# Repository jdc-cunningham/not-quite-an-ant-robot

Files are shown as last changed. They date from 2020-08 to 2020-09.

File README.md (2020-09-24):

# About
My first legged robot. This was not really designed in terms of using math with regard to torque on servos/current draw/etc... as a result it works best on flat surfaces. The motion of the body is also not great since it can't really lift the legs straight up, rather just swing them out then in an arc to move. At this time I'm still working on the control system by phone, I have an ESP8266-01 and it has a websocket server that my phone connects to, then by serial between the ESP and Arduino I can send commands to run specific gaits to move the robot. At the moment I only have some forward gaits, I am still working on improving/writing better "abstractions" for the code eg. passing in an array of servos/ranges into a function to move the servos at the same time. Right now I just have a bunch of loops as a proof of concept.

This is not intended to be replicated, I mean all the parts are here and I'll provide estimates on print but it's not a good design.

This project has been in progress for at least a week, I don't have a repo history because I published my WiFi SSD credentials in the original private repo.

# Status
Pretty much done/abandoned since the body is too weak and dumb to do anything more. It has a run time I could venture to say up to 2.5 hrs on the specified specs but that's absolutely dry. I did a 30 minute non-stop run and it pulled about 500mAh from the battery. This is at 5.5V at the step down buck converter as I was trying to have the servos use around 4.8V. It seems to perform better here than 6V as it was initially. The next project I'm working on the hybrid sensor pack will weigh at least 6oz and I put an 8oz weight on top of the robot and it could not carry it... so that's why I'm kind of going to abandon this robot as is since it's a disappointment in terms of the build/no brain.

# The vision/concept

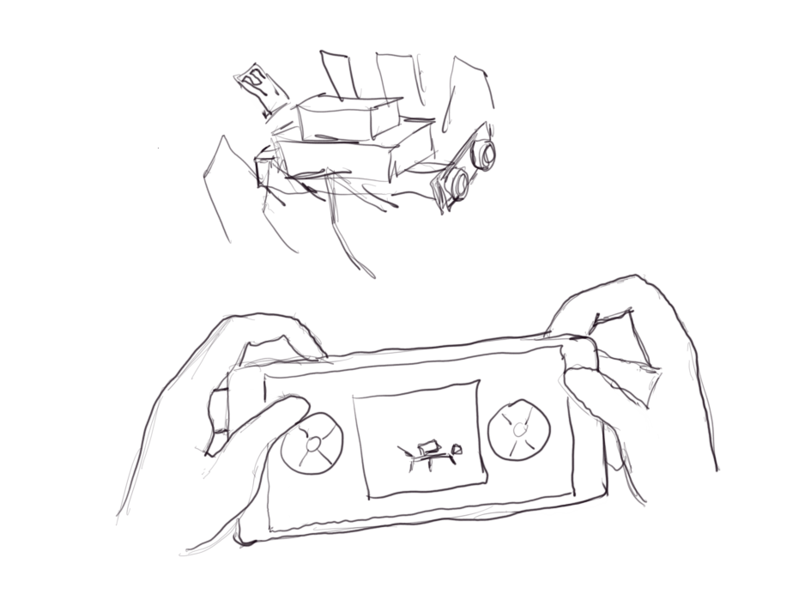
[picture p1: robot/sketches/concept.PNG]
drawing of concept


# Actual - not quite as I foresaw
### Reasons being:
- too slow to control manually, does not have 4 axis of motion only 2(forward/back, left/right)
- telemetry would have been easy with what I'm doing and the embedded `WebGL` aspect would have been overkill as well as a little animation for the controller. Mostly though changing directions, this robot is too weak/stupid to be useful, I can't leave it alone to map a room without thinking it'll get stuck and burn a servo out.

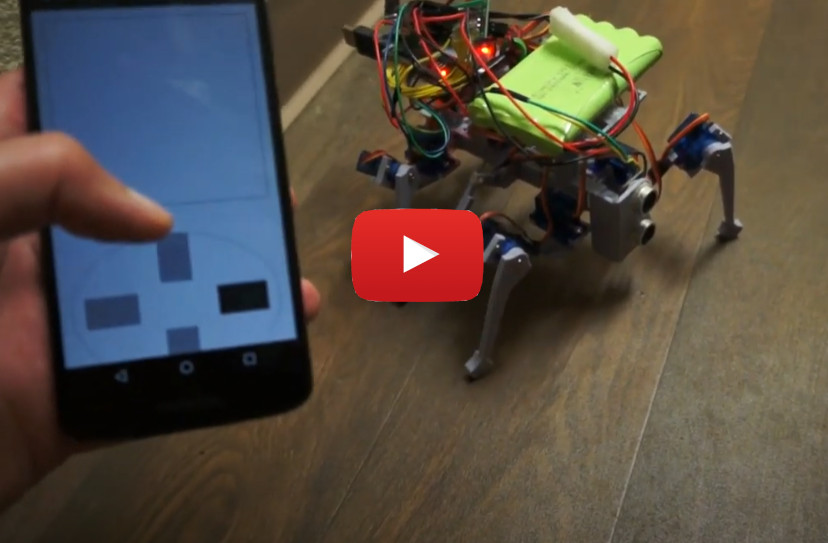
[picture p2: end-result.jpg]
end result (https://youtu.be/18nqn2tWNEw?t=28)


Later on it turns out that having a controller like this while cool is also not practical as the robot is so slow, I'll still build it but it'll be like a "heading hold" type of control.

current build

I did just throw a thing on top to hold the electronics, ideally the CG would be lower, there is clearance below the body, especially since now it's not intended to work on carpet which mine is a little deep eg. `1/2 in` long threads.

While I did design the legs like this(back set not mirrored), they are actually technically "backwards"/not symmetrical... so it has a forward-cg to compensate.

current build side

It has a middle servo pretty much for balance, when it moves forward the middle servo lifts up the middle legs. Anyway with this design as a result I can't do the full tripod-gait, I have some type of modified trypod gait going on. Initially I had a wave-type gait going, where one leg moved at a time but I think that's too slow. It is nuts how much current all the servos pull. I had to use a 2A wall power supply and hardly any of my batteries would work(too heavy/not enough current).

current build back view

Here the servos are not moving very fast(`10ms delay`) and a 2 second overally delay between the forward motion gait see [here](./robot/code/test/all_servos/all_servos.ino).

## Note: it's not as slow as you see above

The servo speed is just set slow there, [here it is near full speed](https://www.youtube.com/watch?v=y_KfgiUq9XE)

# Parts list

- ($18.69 for 10) 9g servo (x9)
- ($15.98 for 3) Arduino Nano
- ($12.98 for 4) ESP8266-01
- ($9.59 for 5) HC-SR04 ultrasonic sensor
- ($12.99 for 5) 5V buck converter for battery (can use UBEC maybe linear regulator as well)
- ($7.85 for 12) 3.3V linear regulator (x2)
- 10K resitor
- ($17.99) 9.6v 8cell 2400mAh NiMh battery pack
- solderable breadboards
- breadboards
- breadboard wires
- 3D printer/filament
- hot/super glue

## Total Unit cost estimate: $50.00
(not including tools eg. 3D printer($200))

### Note: can also use a 7.2v 2 cell battery
After lowering the voltage the servos operated at, it can run on a 2 cell li-ion, I'm using a 2 cell 2600mAh now. It's much lighter(<3oz vs. 6oz)
That gives some extra weight that could be carried.

# Schematic

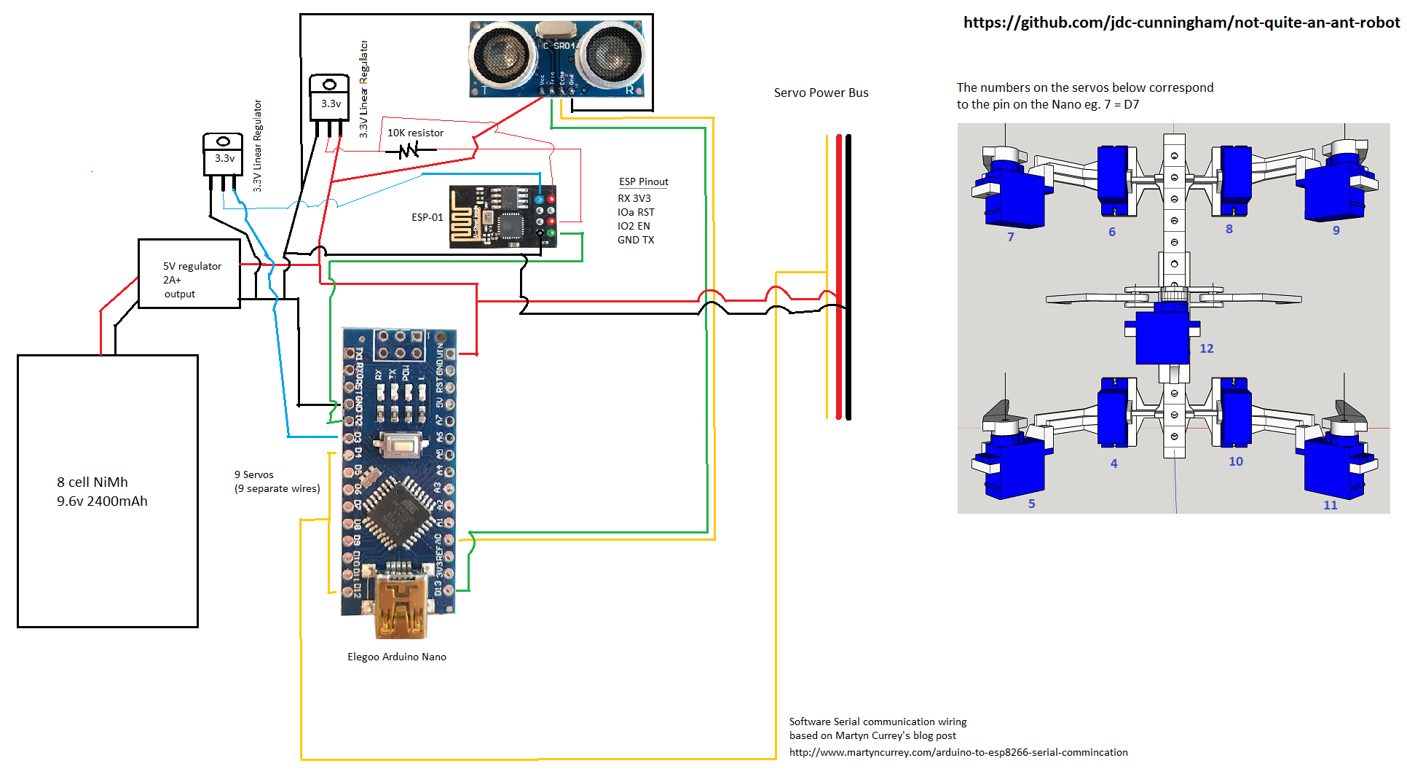
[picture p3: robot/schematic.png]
ms paint wiring diagram


# Feature Completion

- [x] physical body
- [x] basic socket to serial communication
- [ ] rest of the gaits
    - [x] backwards
    - [ ] sideways (crab) - attempt called sway in code
        - doesn't really work(need to be on smooth surface)
    - [x] rotate
    - [ ] roll
        - similar to crab walk, again problem of servos being weak
- [x] mobile controller
    - very basic design, spent like 2 hours
- [ ] add IMU (9-axis)
    - not done on this robot, maybe added later assuming light enough
- [x] add ultrasonic sensor on front
    - current code intercepts commands and makes robot turn left if something is within 7" of front

# Print times (0.2mm quality 20% infill)
- 49 mins main servo mount for swivel arms
- 2 hrs 42 mins middle lift legs
- 4 hrs 20 mins top group
- 3 hrs 14 mins test stand
- 1 hr 29 mins outer pitch legs
- 1 hr 26 mins 1 swivel arm
- 1 hr 34 mins main stick with holes

## Update
I would suggest printing the legs(pitch and swivel) thicker as they experience the most stress. This is only really a problem on carpet. I am printing out these foot cups which may help alleviate the stress on the legs but still it may be a good idea to increase that thickness(will need to reslice).

# Software

The parts were designed with Google SketchUp. I used a plugin to export the STL file(as well as a solid part inspector plugin) then used Cura to slice the parts. Take note of parts that need supports, you have to turn that on in Cura. Parts are printed with a Creality Ender 3 Pro.

# Warning

The servo horn spline I have here is bad, they slip. I traced/made my own from a photo I took. I ended up having to use long screws and super glue to try and make them not slip. Also the design is generally bad where the servos are directly holding the load vs. just transfering motion. And overall the design is bad as I mentioned with how it can move. I think you need more servos but it's nuts thinking each leg would have at least 3 servos and a true hexapod would have 18 servos right there.

# Thoughts

Overall it is a fun project, learned a lot. It has a ways to go code wise and will serve as a platform for other work.

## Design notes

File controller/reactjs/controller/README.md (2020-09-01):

# About the controller
This is a basic controller, I created a different version initially but triangles in html/css are kind of a hack so the last triangle overlaps the rest... problems with clicks. It's not an impossible thing to solve eg. use SVG or background images, etc... but yeah. Also the math since I didn't have something to bind clicks to, this is not just a quadrant it's a diagonal thing going on for the original design below. I ended up just going with a basic `+` style controller. It's also not responsibly styled or anything, I probably spent 2 hrs on this controller so yeah it's trash but it does work. When the robot is turned on __first__ your phone or computer that's looking at the deployed static files of this controller will connect to the robot and steer it. The ultrasonic sensor onboard will interrupt your command and avoid an obstacle if it detects one within 7 inches(roughly half the box the robot takes up/uses to rotate).

Also I have not gotten to the interface/telemetry aspect. It's kind of pointless at this time for this project since I can't leave this project alone(it can get stuck, flip over, etc... strain the servos). For example the center servo got so hot(not sure if it was a dud or not, hasn't happened since) but it got so hot it started to melt the plastic mount(3D printed).

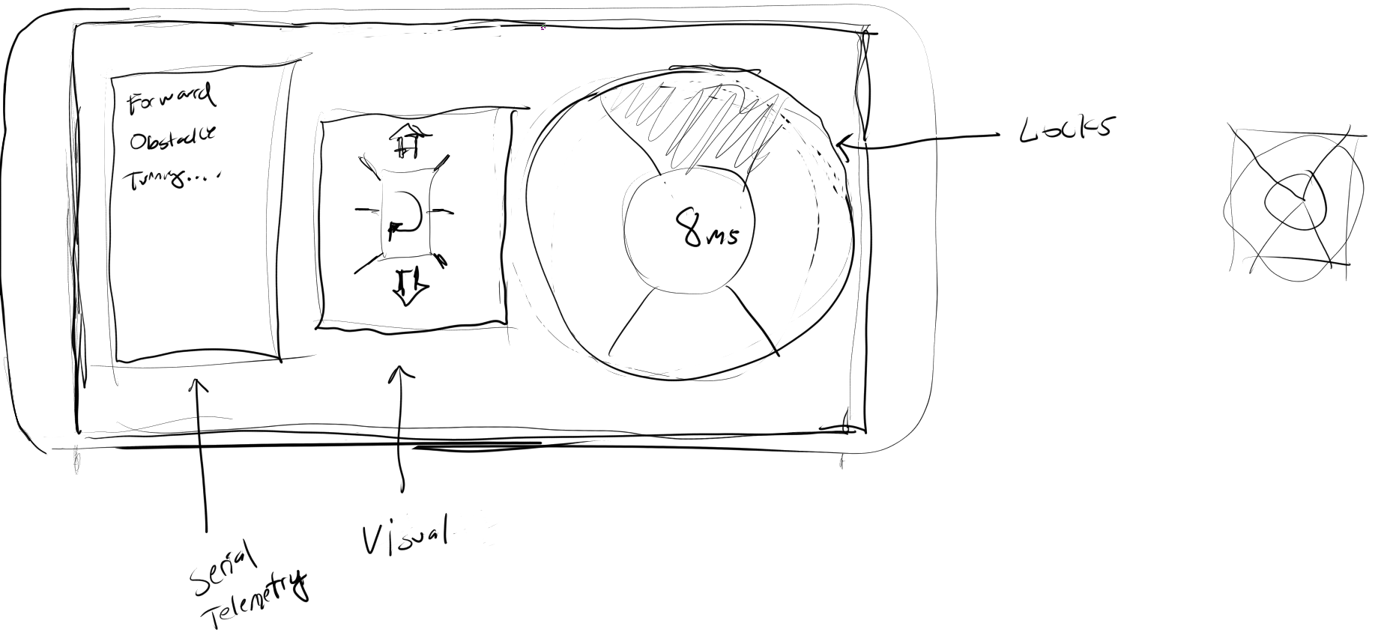
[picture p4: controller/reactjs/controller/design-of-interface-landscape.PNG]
controller thoughts


Anyway instead of the above you just have this lol. But yeah some telemetry would be possible by the serial onboard but since it's software serial at `115200` (trash data) you'd probably have to do some enumeration like I did which I don't know how useful that is.

The other aspect that's missing here is a front-end IP scanner because the IP may change if your router re-assigns the device. So you'd have to manually put in existing/known ip's then the mobile controller would scan the possible open ones and try to connect by socket.

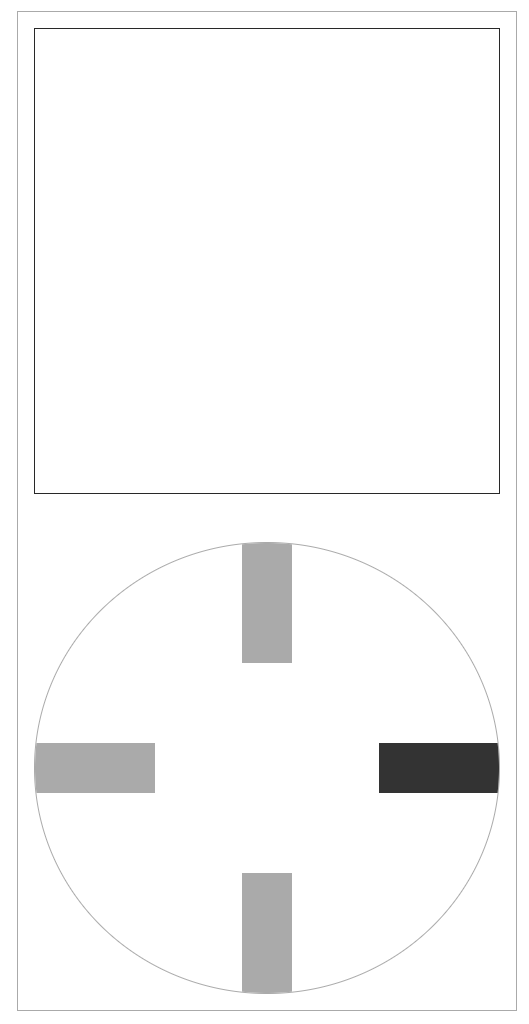
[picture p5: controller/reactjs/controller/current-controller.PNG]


# To use
Anyway if anyone actually tries to use this. You'll have to change the IP in the `App.js` to match your ESP's IP that's hosting the websocket server. Then do `npm run build` that'll generate your static files(assumes you have `node/npm/npx` installed haha). I can see how you make "useable code".

This project was bootstrapped with [Create React App](https://github.com/facebook/create-react-app).

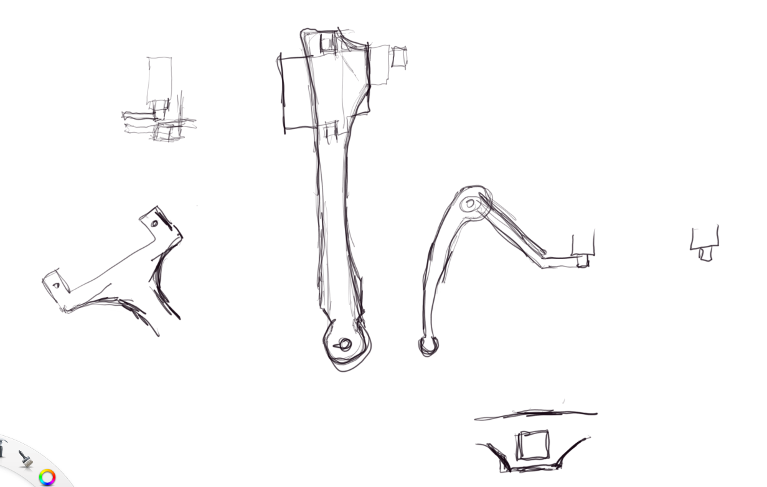
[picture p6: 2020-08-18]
robot/sketches/leg-design.PNG

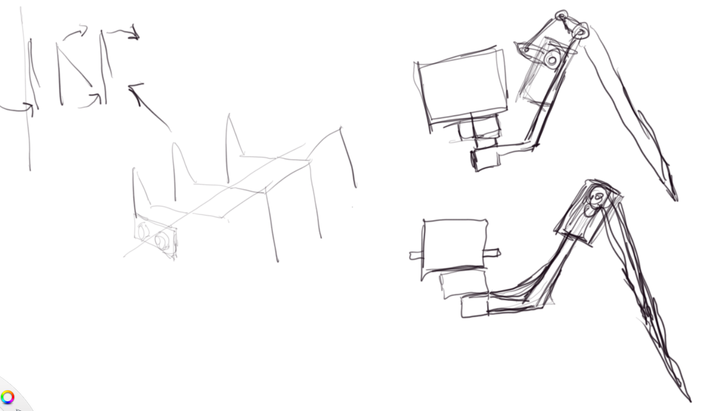
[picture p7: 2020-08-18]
robot/sketches/concept2.PNG

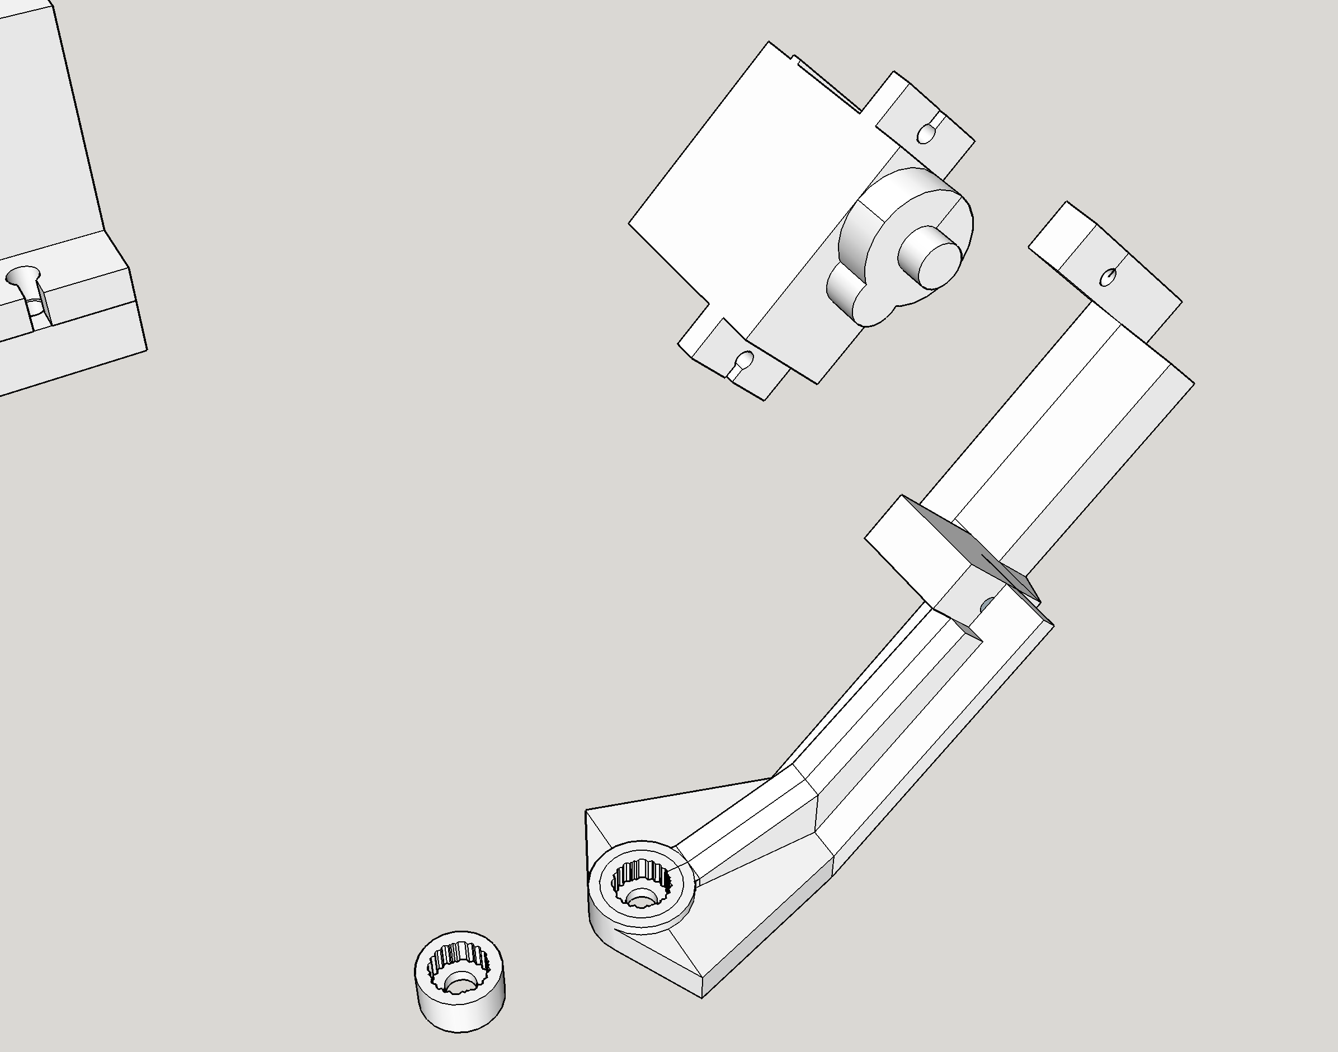
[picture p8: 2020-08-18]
robot/screenshots/no-way.png

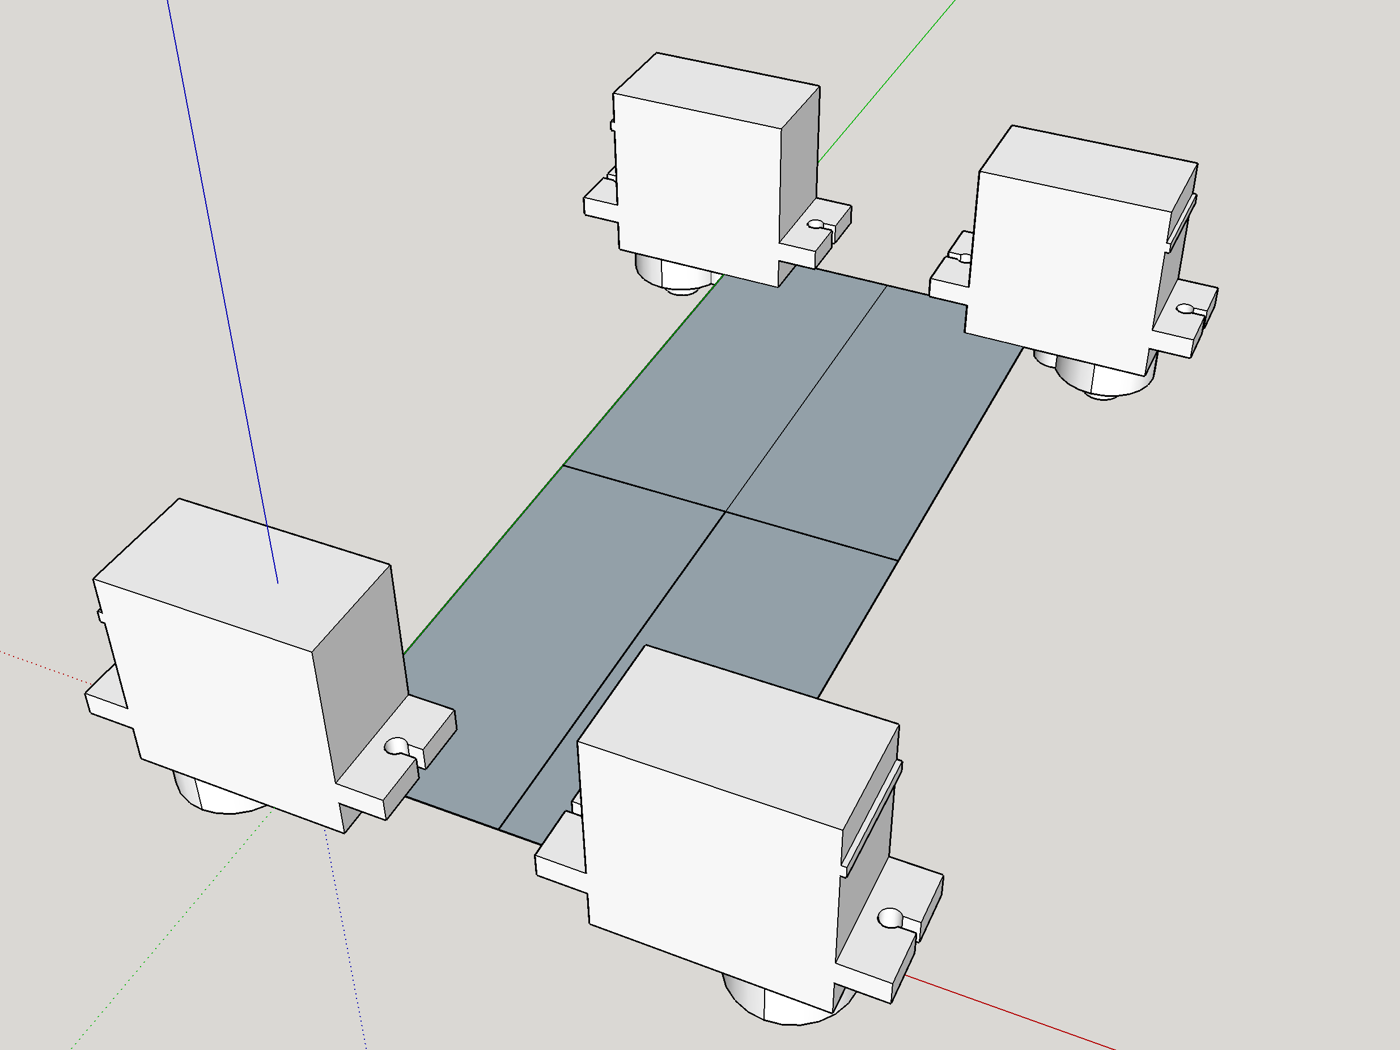
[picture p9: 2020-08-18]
robot/screenshots/chasis-config-1.png

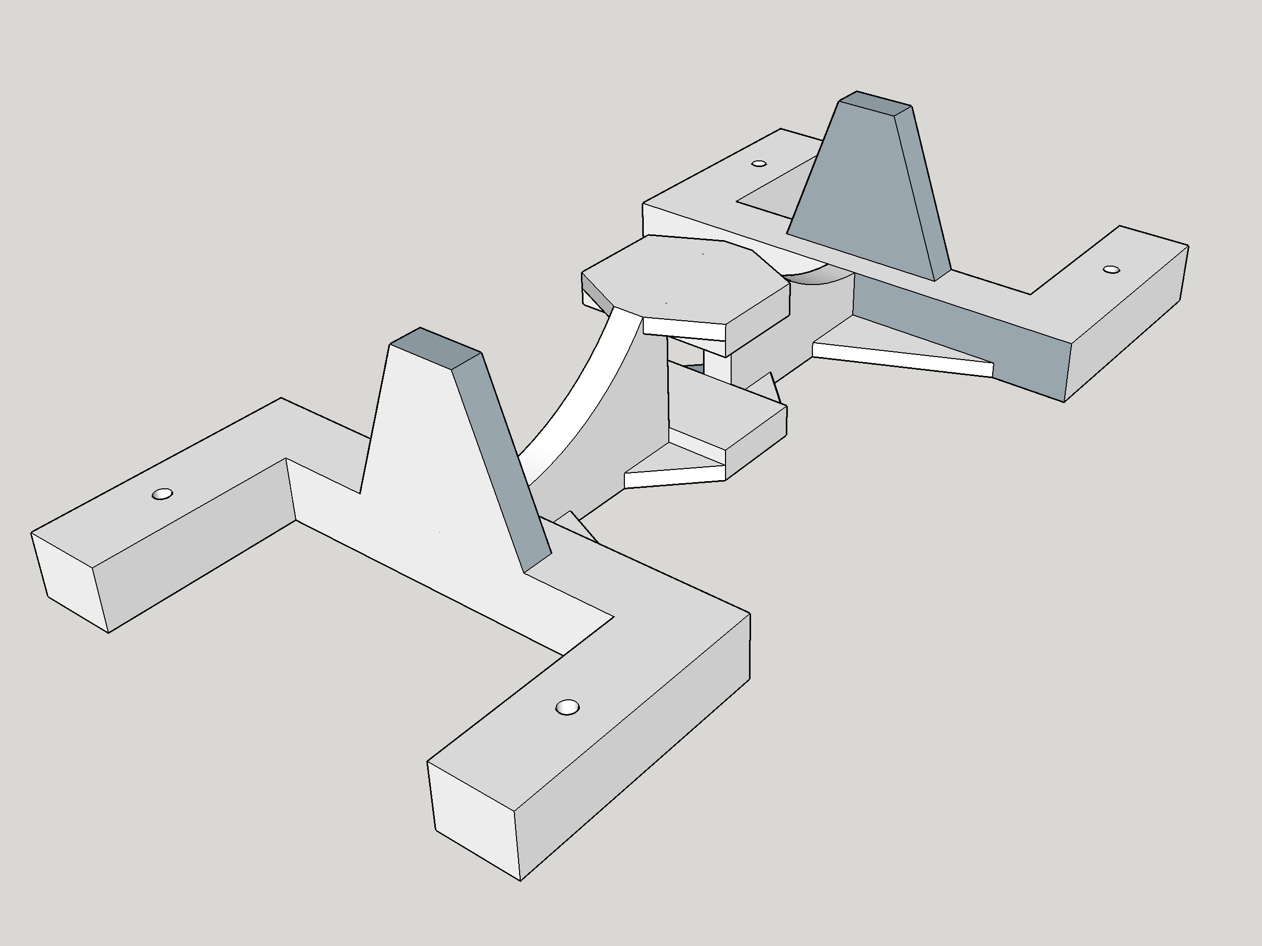
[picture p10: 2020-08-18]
robot/screenshots/horizontal-swivel-servo-mount.png

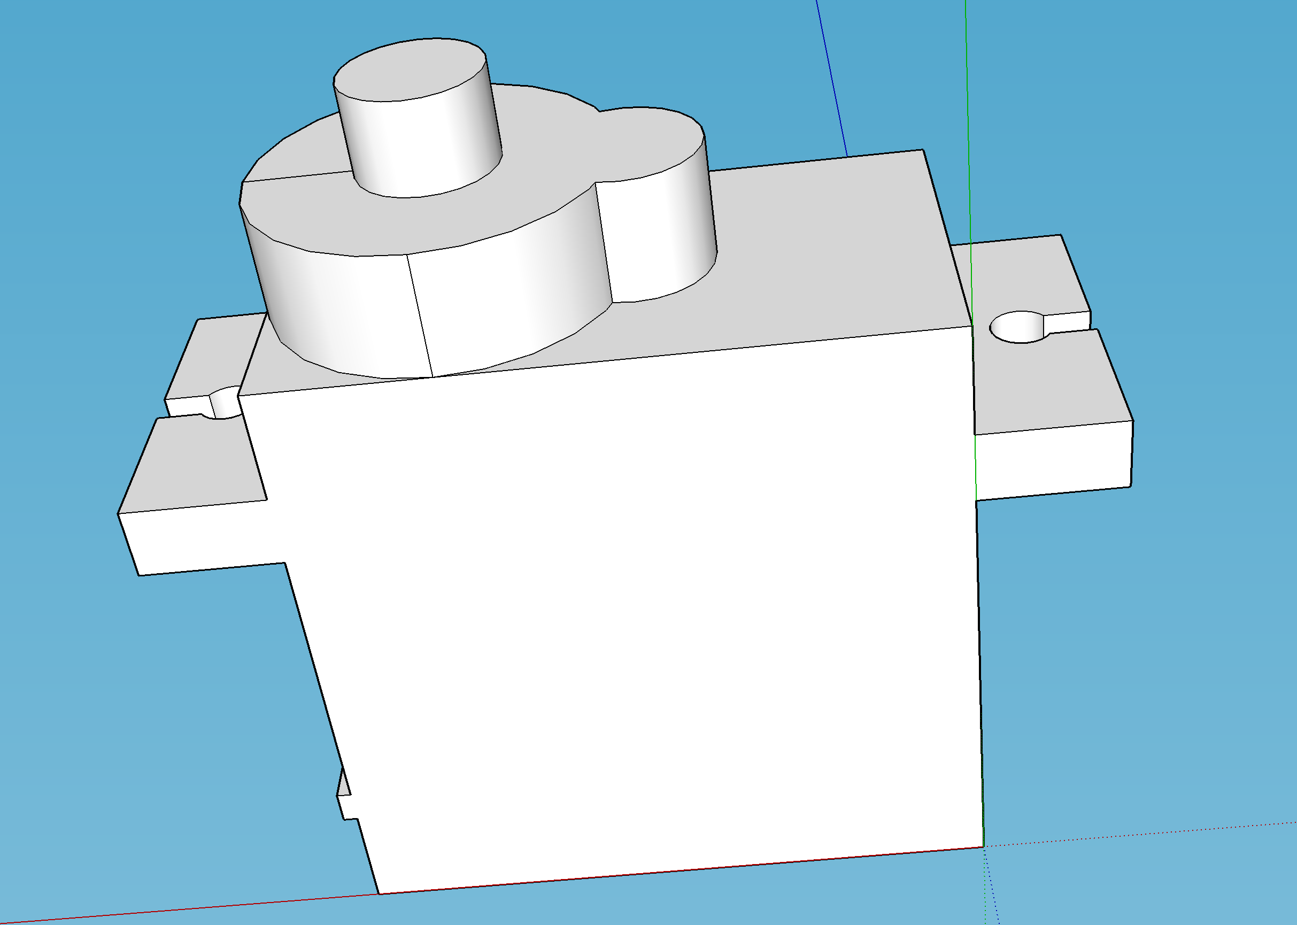
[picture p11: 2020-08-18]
robot/screenshots/sg90.png

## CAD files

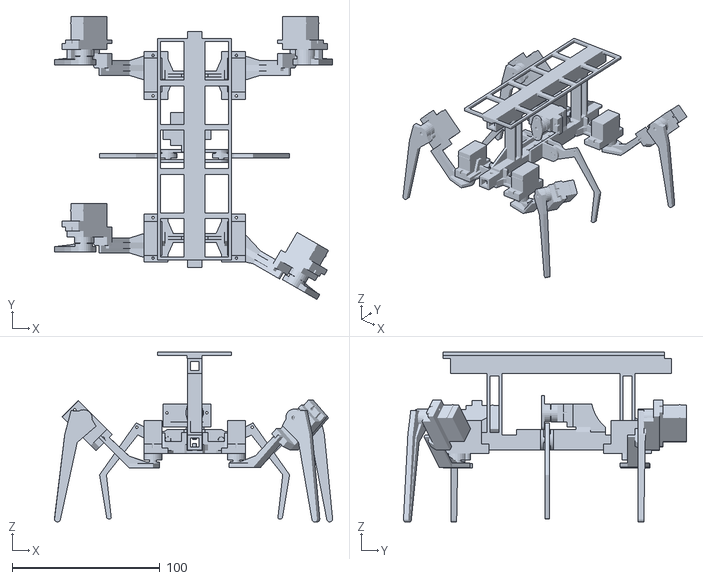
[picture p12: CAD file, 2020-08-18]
robot/3d-files/full-body-prototype.stl
188.5 x 191.8 x 115.2

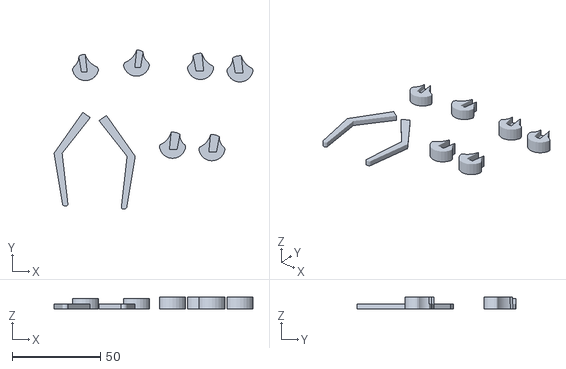
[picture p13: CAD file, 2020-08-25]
robot/3d-files/alt-foot-cups-more-middle-legs.stl
113.0 x 90.4 x 7.00

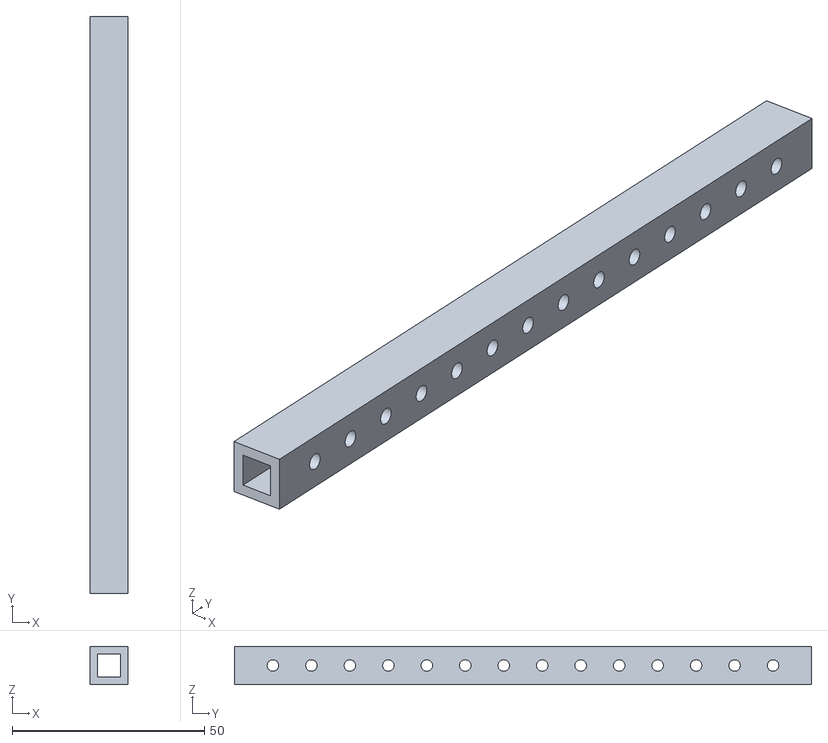
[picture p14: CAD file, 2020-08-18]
robot/3d-files/wh-2mm-by-10mm-stick.stl
10.0 x 150.0 x 10.0

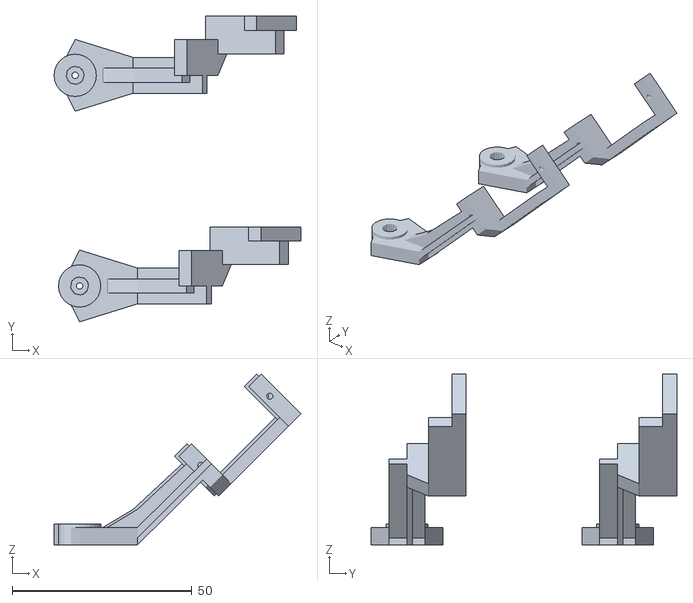
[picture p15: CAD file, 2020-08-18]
robot/3d-files/l-swivel-arms.stl
68.8 x 85.1 x 47.6

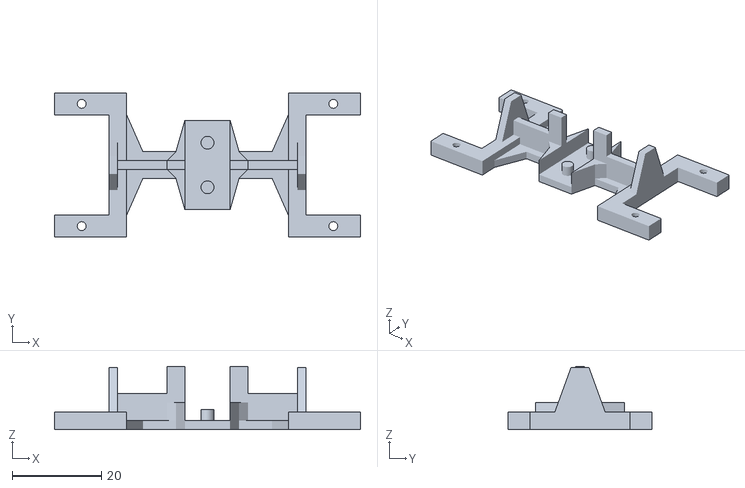
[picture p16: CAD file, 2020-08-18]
robot/3d-files/servo-arm.stl
68.7 x 32.3 x 14.2

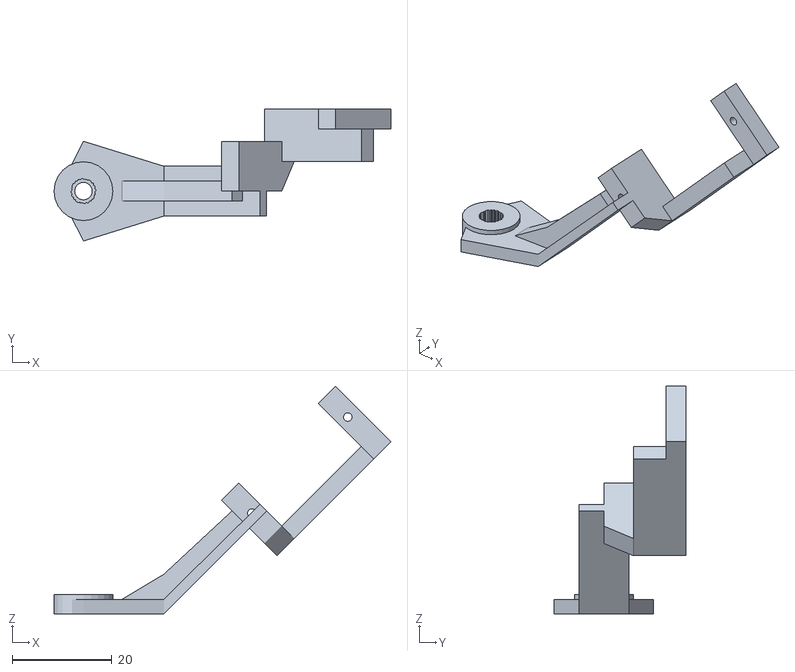
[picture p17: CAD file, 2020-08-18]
robot/3d-files/swivel-arm.stl
67.6 x 26.5 x 45.6

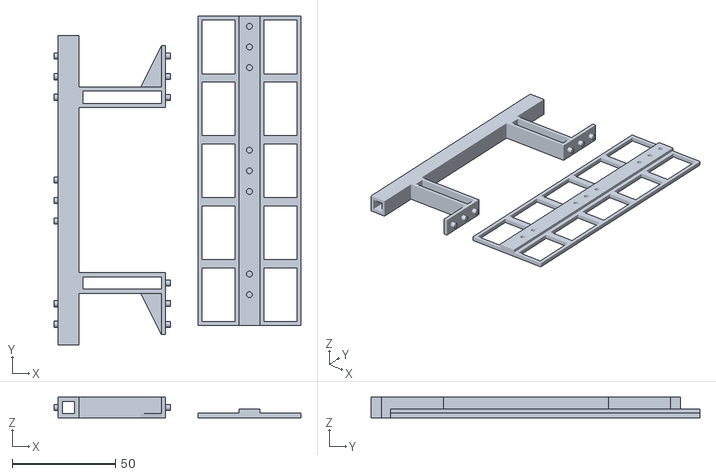
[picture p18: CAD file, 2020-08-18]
robot/3d-files/top-layer.stl
119.7 x 159.4 x 10.0

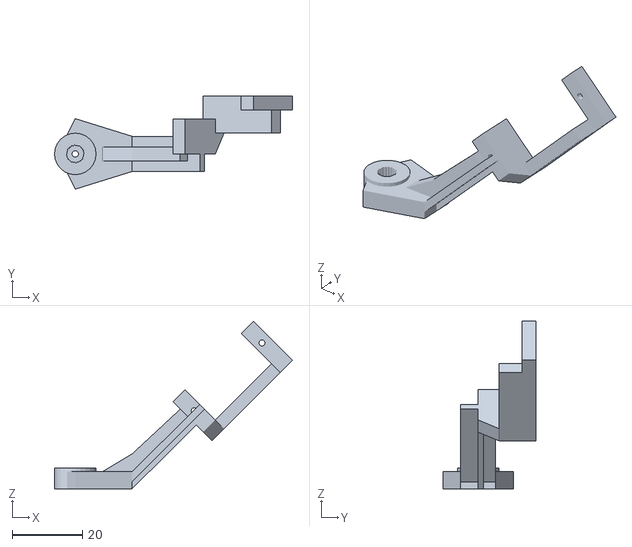
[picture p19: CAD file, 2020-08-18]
robot/3d-files/l-swivel-arm.stl
67.6 x 26.5 x 47.6

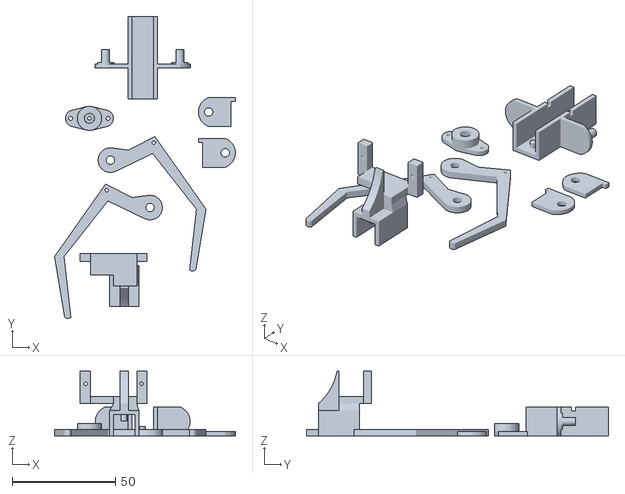
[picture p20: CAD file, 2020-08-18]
robot/3d-files/mid-lift-legs.stl
87.7 x 146.4 x 31.3

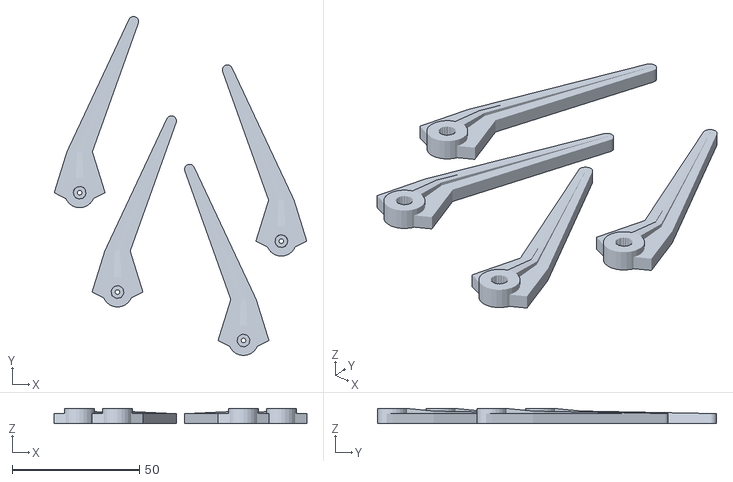
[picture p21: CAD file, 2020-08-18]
robot/3d-files/pitch-legs.stl
99.2 x 133.1 x 5.90

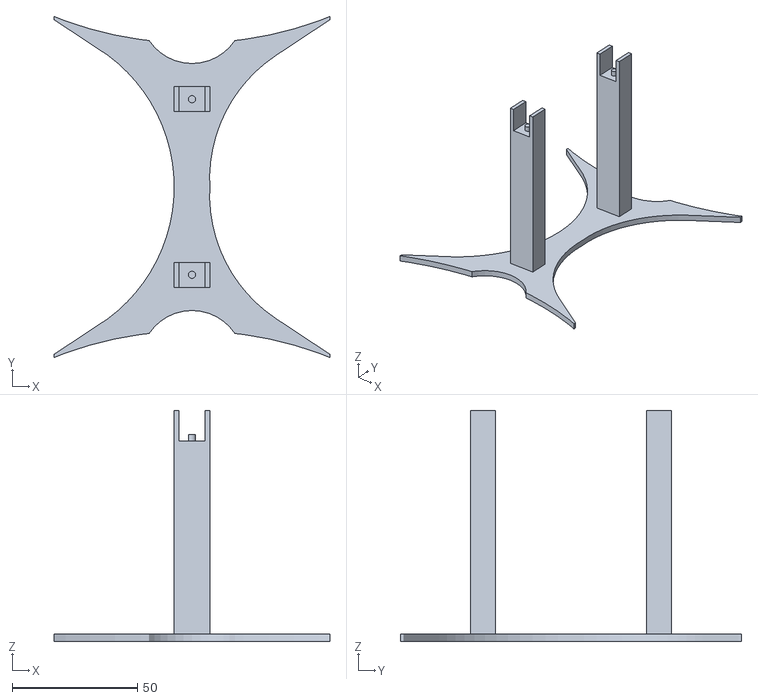
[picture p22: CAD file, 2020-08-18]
robot/3d-files/test-stand.stl
110.0 x 136.0 x 92.2

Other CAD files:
robot/3d-files/half-arm.stl
robot/3d-files/r-swivel-arms.stl
robot/3d-files/alt-foot-cups-more-middle-legs.skp
robot/3d-files/full-body-prototype.skp
robot/3d-files/full-body-prototype~.skp
robot/3d-files/half-arm.skp
robot/3d-files/half-arm~.skp
robot/3d-files/mid-lift-legs.skp
robot/3d-files/mid-lift-legs~.skp
robot/3d-files/pitch-legs.skp
robot/3d-files/pitch-legs~.skp
robot/3d-files/r-swivel-arms.skp
robot/3d-files/sg90.skp
robot/3d-files/sg90~.skp
robot/3d-files/swivel-arm.skp
robot/3d-files/swivel-arm~.skp
robot/3d-files/test-stand.skp
robot/3d-files/top-layer.skp
robot/3d-files/top-layer~.skp

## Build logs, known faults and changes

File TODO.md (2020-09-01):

- [ ] mobile controller
    - [ ] basic left display, middle GUI showing robot state, right D-pad
        - [ ] switchable eg. left/right
    - [ ] telemetry
        - [ ] rquires ESP and Nano modification
            - [ ] updates middle UI above and prints on left

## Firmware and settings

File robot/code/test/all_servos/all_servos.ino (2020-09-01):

/**
 * all servos plugged in
 * visual:
 * 
 *     FLO          FRO
 *         FLI  FRI
 *         
 *         BLI  BRI
 *     BLO          BRO
 *
 */

#include <SoftwareSerial.h>
#include <Servo.h>
SoftwareSerial ESPserial(2, 3); // rx tx
Servo frontRightInnerServo;
Servo frontRightOuterServo;
Servo frontLeftInnerServo;
Servo frontLeftOuterServo;
Servo backRightInnerServo;
Servo backRightOuterServo;
Servo backLeftInnerServo;
Servo backLeftOuterServo;
Servo middleServo;

int servoMotionDelay = 6; // how fast the servo moves a deg in ms
int usSensorTrigPin = 13;
int usSensorEchoPin = A0;
int usSensorTravelDuration;
int usSensorMeasuredDistance;
int avoidRotateCounter = 0;
bool avoidRotateDirectionLeft = true;

void setup() {
  setAndCenterServos();
  Serial.begin(115200);
  ESPserial.begin(115200);

  // setup ultrasonic sensor
  pinMode(usSensorTrigPin, OUTPUT);
  pinMode(usSensorEchoPin, INPUT);
}

String commandStr;
int appendCounter = 0;
bool commandMatch = false;
bool motionInProgress = false;
String commIntRange = "23456789";

void loop() {
  /**
  * current commands:
  * F - forward
  * L - rotate left
  * R - rotate right
  * B - backwards
  * # - set speed of servo eg. ms delay per degree rotation
  * Software Serial is not reliable at 115200, even checking 2 characters has too many errors
  */
  while (ESPserial.available()) {
    char c = ESPserial.read();
    commandStr += c;
    appendCounter += 1;

    Serial.println(commandStr);

    if (appendCounter > 1) {
      commandStr = "";
      appendCounter = 0;
    } else {
      usSensorPing();
      if (obstacleDetected()) {
        rotateLeft();
        return;
      }

      if (commandStr.indexOf("F") > -1 && !motionInProgress) {
        commandMatch = true;
        moveForward();
      } else if (commandStr.indexOf("L") > -1 && !motionInProgress) {
        commandMatch = true;
        rotateLeft();
      } else if (commandStr.indexOf("R") > -1 && !motionInProgress) {
        commandMatch = true;
        rotateRight();
      } else if (commandStr.indexOf("B") > -1 && !motionInProgress) {
        commandMatch = true;
        moveBackward();
      } else if (commIntRange.indexOf(commandStr) > -1) {
         // 2 is really fast relatively, and anything above 10 is really slow
        if (commandStr.toInt() >= 2 && commandStr.toInt() < 10) { // should go up to 10 but 1 char is easier to check
          servoMotionDelay = commandStr.toInt();
        }
      }

      if (commandMatch) {
        commandStr = "";
        appendCounter = 0;
        commandMatch = false;
      }
    }
  }

  // moveForward();
  // moveAllLegsBackward();
  // moveBackward();
  // setAndCenterServos();
  // rotateLeft();
  // rotateRight();
  // swayLeft();

  // delay(60000);
}

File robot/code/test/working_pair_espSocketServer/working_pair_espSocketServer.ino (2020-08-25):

// using library https://github.com/gilmaimon/ArduinoWebsockets
#include <ArduinoWebsockets.h>
#include <ESP8266WiFi.h>

using namespace websockets;
WebsocketsServer socketServer;

bool clientActive = false;
int serverPollDelay = 250;

void connectToWiFi() {
  WiFi.begin("SSID", "SSIDPASS");

  while (WiFi.status() != WL_CONNECTED) {
    delay(250);
    Serial.println("Waiting for connection");
  }

  Serial.println("Connected!");
  Serial.println("Starting socket server...");
  socketServer.listen(80);
}

void setup() {
  Serial.begin(115200);
  connectToWiFi();
}

void loop() {
  Serial.println("poll");

  if (!clientActive) {
    auto client = socketServer.accept();
    clientActive = true;
 
    if (client.available()) {
      for (int i = 0; i < 60000; i++) { // 1 minute poll for messages
        if (client.available()) {
          auto msg = client.readBlocking();
          if (msg.data().length() > 0) {
            Serial.println(msg.data());
          }
          // client.send(msg.data()); // to mobile controller
        } else {
          break;
        }
        delay(1);
      }
      clientActive = false;
    }
  }
}

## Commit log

2020-08-18 first public files for body
    [full-body-prototype.skp, full-body-prototype.stl, full-body-prototype~.skp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]
2020-08-23 Update README.md
    added note about T H I C C er legs
2020-08-25 3dfile and code updates
    [alt-foot-cups-more-middle-legs.skp, alt-foot-cups-more-middle-legs.stl]
2020-08-25 clear esp serial buffer correctly
    [motion_functions.ino]
2020-09-01 adding current code and schematic on how to wire parts
